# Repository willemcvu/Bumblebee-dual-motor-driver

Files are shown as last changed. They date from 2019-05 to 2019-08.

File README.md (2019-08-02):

**_NOTE: Everything here is still actively in development, and is mostly untested. Firmware has not been written; BOMs have not been created. If you'd like to use something here, I would suggest waiting until I have tested all hardware and written firmware._**

**All boards below will be available for sale bare or assembled at some point in the near future, likely on Tindie. For now, feel free to start an issue if you're interested in buying a board.**

Kicad and Arduino sources for the Bumblebee seris of Arduino-compatible dual-motor control boards, all designed to be retrofitable in the Fisher-Price WildThing to provide alternative control means for wheelchair adaption.

There are three different boards, each with discinct purposes.

# Bumblebee-board
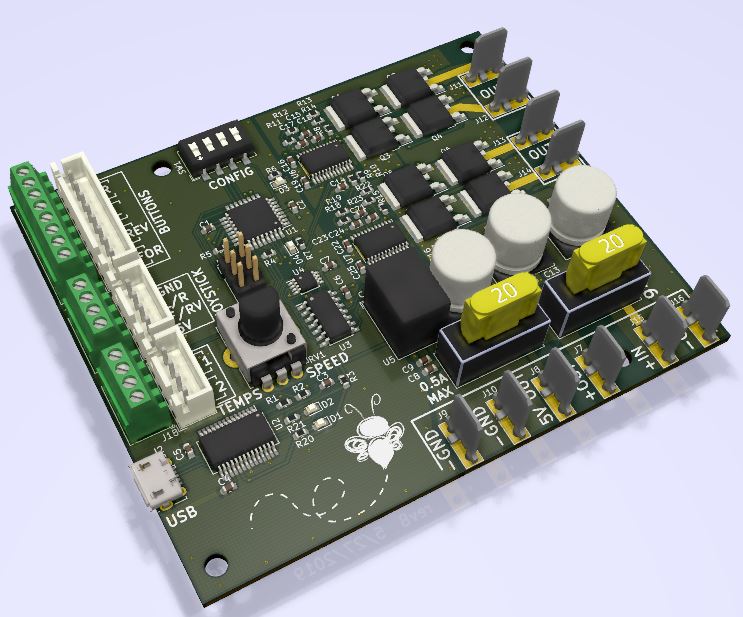
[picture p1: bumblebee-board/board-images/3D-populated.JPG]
bumblbee-board


This is the main board, and is designed to be a drop-in replacement of the stock WildThing control board. There are two complete H-bridge motor drivers using the A4940 motor driver. The uC is the AtMega328P, with an FTDI USB interface for complete Arduino functionaliy. Connectors for motor and power match those on the stock control board (they mate to standard 1/4" automotive blade terminals), so no crimping or soldering is needed.

Other features include:
* Dual inputs: buttons or joystick
* Choice of JST XH or screw terminals for button/joystick inputs
* On-the-fly configuration via DIP switch
* Potentiometer for speed limiting adjustment
* Built-in fusing
* Fused blade-type 12V and 5V outputs, as well as two extra grounds
* Instructions on the back, as well as Arduino pin equivelancies for the terminal blocks

This board has an operating voltage of 7V-24V, although the max could be raised by changing the 470uF caps to higher-voltage rated caps.

# Bumblebee-adapter
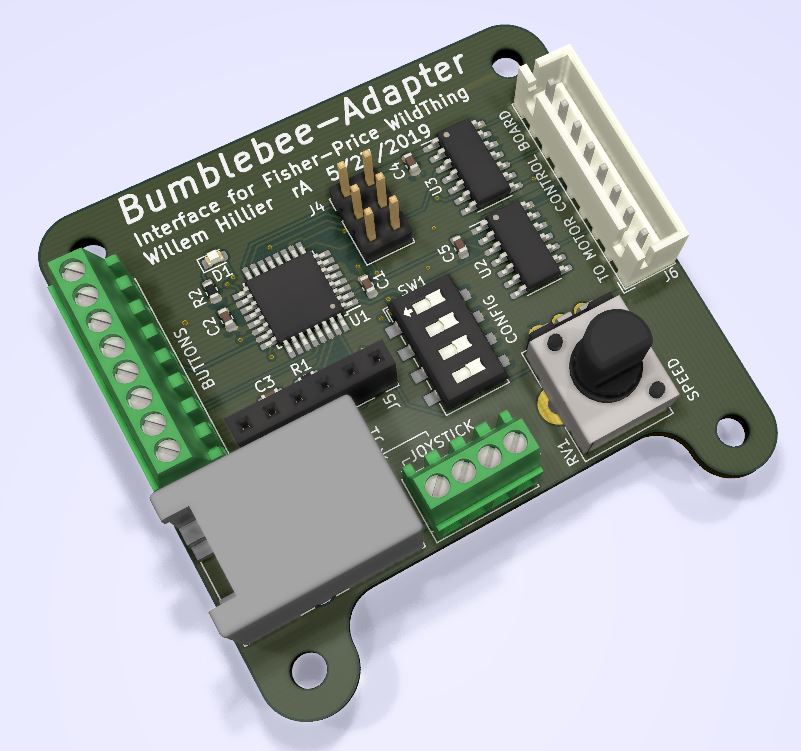
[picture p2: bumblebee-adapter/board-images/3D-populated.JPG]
bumblebee-adapter


This is probably the ultimate solution for a configurable, low-cost WildThing controller.

This board does not directly drive motors. Instead, it plugs into the joystick headers on the original control board and emulates their signals using two dual-channel SPI DACs. The speed limiting is still controllable via the original button under the seat using this method, and the seat safety switch remains intact.

It does not have onboard USB (due to cost), but has an "FTDI" port for easy programming/configuration with any generic USB-to-serial cable.

It also sports an RJ25 port for joystick input, in addition to a set of 2.54mm holes that can be used either for a terminal block or for a JST XH connector. I'll be designing a 3D-printable joystick unit with a matching RJ25 port at some point in the near future.

# Bumblebee-compact
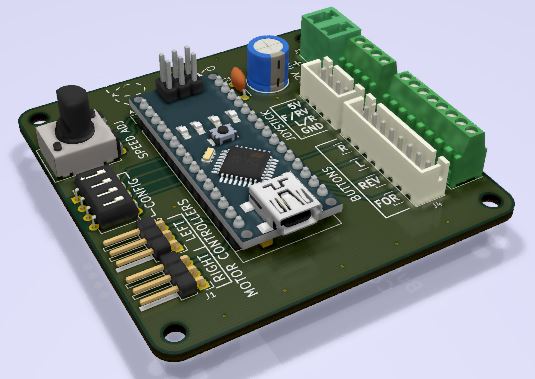
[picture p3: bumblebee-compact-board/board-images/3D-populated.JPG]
bumblebee-compact


This very simple board is designed to be a very low-cost, easy-to-solder board that drives external motor controllers, such as RC electronic speed controls (ESCs). All components are through-hole, and the total cost of assembling this should only be around $15.

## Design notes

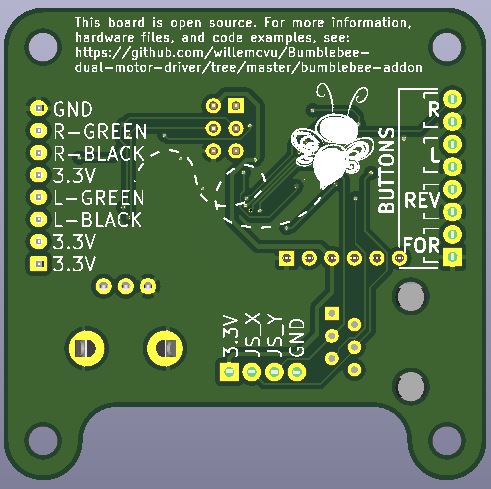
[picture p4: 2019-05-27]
bumblebee-adapter/board-images/back-populated.JPG

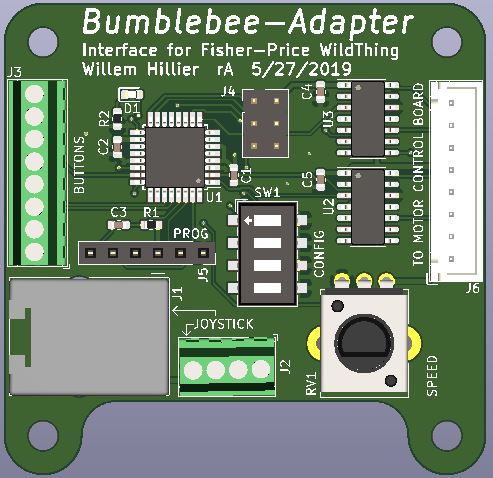
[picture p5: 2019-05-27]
bumblebee-adapter/board-images/front-populated.JPG

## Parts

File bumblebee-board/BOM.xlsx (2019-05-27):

Id | Designator | Package | Quantity | Designation | Manufacturer | PN
4 | J11 | TE_1217861-1 | 9 | MOTOR1_A | TE | 1217861-1
6 | C13,C11,C12 | C_Elec_10x10.2 | 3 | 470u |  | EEV477M025S9PAA
7 | C24,C25,C23,C17,C18,C19 | C_0603_1608Metric | 6 | 1u | NIC Components | NMC0603Y5V105Z16TRPF
8 | C22,C20,C1,C2,C3,C4,C5,C6,C7,C9,C10,C14,C16 | C_0603_1608Metric | 13 | 0.1u
9 | C21,C8,C15 | C_0603_1608Metric | 3 | 10u
10 | R19,R18,R16,R17,R10,R11,R12,R13 | R_0603_1608Metric | 8 | 27 | NIC Components | NRC06F27R0TRF
11 | U7,U6 | HTSSOP-24-1EP_4.4x7.8mm_P0.65mm_EP3.4x7.8mm_Mask2.4x4.68mm | 2 | A4940KLPTR-T | ALLEGRO | A4940KLPTR-T
12 | Q7,Q6,Q5,Q8,Q1,Q2,Q3,Q4 | TO-252-2 | 8 | Q_NMOS_GDS | Infineon | IRFR3410TRLPBF
15 | R14,R3,R4,R5,R8 | R_0603_1608Metric | 5 | 10k
16 | R15,R9 | R_0603_1608Metric | 2 | 82k | NIC Components | NRC06J823TRF
17 | D1 | LED_0603_1608Metric | 1 | RX
18 | D2 | LED_0603_1608Metric | 1 | TX
19 | D3,D4 | LED_0603_1608Metric | 2 | LED
20 | J5,J18 | JST_XH_B4B-XH-A_1x04_P2.50mm_Vertical | 2 | JST-XH
21 | J6 | JST_XH_B8B-XH-A_1x08_P2.50mm_Vertical | 1 | JST-XH
28 | R1,R2,R6,R7,R20,R21 | R_0603_1608Metric | 6 | 1k
29 | SW1 | SW_DIP_SPSTx04_Slide_6.7x11.72mm_W6.73mm_P2.54mm_LowProfile_Jpin | 1 | SW_DIP_x04 | CTS | 219-4LPST
30 | U1 | TQFP-32_7x7mm_P0.8mm | 1 | ATmega328P-AU
31 | U2 | SSOP-28_5.3x10.2mm_P0.65mm | 1 | FT232RL | FTDI | FT232RL-TUBE
32 | U3 | SOIC-14_3.9x8.7mm_P1.27mm | 1 | 74LS08 | Texas Instruments | SN74LS08D
33 | U4 | TSSOP-8_3x3mm_P0.65mm | 1 | 74LVC2G240 | Nexperia | 74LVC2G240DC,125
34 | U5 | Converter_DCDC_RECOM_R-78E-0.5_THT | 1 | R-78E5.0-0.5 | Recom | R-78E5.0-0.5
35 | J1 | PinHeader_2x03_P2.54mm_Vertical | 1 | ICSP
36 | F1,F2 | Fuseholder_Blade_Mini_Keystone_3568 | 2 | 0.5A
38 | J4 | TerminalBlock_TE_282834-8_1x08_P2.54mm_Horizontal | 1 | HEADER
39 | J3,J17 | TerminalBlock_TE_282834-4_1x04_P2.54mm_Horizontal | 2 | HEADER
40 | J2 | USB_Micro-B_Molex-105017-0001 | 1 | USB_B_Micro | Molex | 105017-0001
41 | RV1 | Potentiometer_Bourns_PTV09A-1_Single_Vertical | 1 | R_POT_US | Bourns | PTV09A-4020F-B103

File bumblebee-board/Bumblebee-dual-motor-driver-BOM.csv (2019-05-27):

Id | Designator | Package | Quantity | Designation | Supplier and ref
1 | G*** | vtLogo15mm | 1 | LOGO
2 | REF**,REF**,REF**,REF** | MountingHole_3.2mm_M3 | 4 | MountingHole_3.2mm_M3
3 | SW1 | dipLOGO | 1 | SW_DIP_x04
4 | J11 | TE_1217861-1 | 1 | MOTOR1_A
5 | G***,G*** | bumblebee_logo | 2 | LOGO
6 | C13,C11,C12 | C_Elec_10x10.2 | 3 | 470u
7 | C24,C25,C23,C17,C18,C19 | C_0603_1608Metric | 6 | 1u
8 | C22,C20,C1,C2,C3,C4,C5,C6,C7,C9,C10,C14,C16 | C_0603_1608Metric | 13 | 0.1u
9 | C21,C8,C15 | C_0603_1608Metric | 3 | 10u
10 | R19,R18,R16,R17,R10,R11,R12,R13 | R_0603_1608Metric | 8 | 27
11 | U7,U6 | HTSSOP-24-1EP_4.4x7.8mm_P0.65mm_EP3.4x7.8mm_Mask2.4x4.68mm | 2 | A4940KLPTR-T
12 | Q7,Q6,Q5,Q8,Q1,Q2,Q3,Q4 | TO-252-2 | 8 | Q_NMOS_GDS
13 | J13 | TE_1217861-1 | 1 | MOTOR2_A
14 | J14 | TE_1217861-1 | 1 | MOTOR2_B
15 | R14,R3,R4,R5,R8 | R_0603_1608Metric | 5 | 10k
16 | R15,R9 | R_0603_1608Metric | 2 | 82k
17 | D1 | LED_0603_1608Metric | 1 | RX
18 | D2 | LED_0603_1608Metric | 1 | TX
19 | D3,D4 | LED_0603_1608Metric | 2 | LED
20 | J5,J18 | JST_XH_B4B-XH-A_1x04_P2.50mm_Vertical | 2 | JST-XH
21 | J6 | JST_XH_B8B-XH-A_1x08_P2.50mm_Vertical | 1 | JST-XH
22 | J7 | TE_1217861-1 | 1 | 12V_OUT
23 | J8 | TE_1217861-1 | 1 | 5V_OUT
24 | J9,J10 | TE_1217861-1 | 2 | GND
25 | J12 | TE_1217861-1 | 1 | MOTOR1_B
26 | J15 | TE_1217861-1 | 1 | MAIN+
27 | J16 | TE_1217861-1 | 1 | MAIN-
28 | R1,R2,R6,R7,R20,R21 | R_0603_1608Metric | 6 | 1k
29 | SW1 | SW_DIP_SPSTx04_Slide_6.7x11.72mm_W6.73mm_P2.54mm_LowProfile_JPin | 1 | SW_DIP_x04
30 | U1 | TQFP-32_7x7mm_P0.8mm | 1 | ATmega328P-AU
31 | U2 | SSOP-28_5.3x10.2mm_P0.65mm | 1 | FT232RL
32 | U3 | SOIC-14_3.9x8.7mm_P1.27mm | 1 | 74LS08
33 | U4 | TSSOP-8_3x3mm_P0.65mm | 1 | 74LVC2G240
34 | U5 | Converter_DCDC_RECOM_R-78E-0.5_THT | 1 | R-78E5.0-0.5
35 | J1 | PinHeader_2x03_P2.54mm_Vertical | 1 | ICSP
36 | F1 | Fuseholder_Blade_Mini_Keystone_3568 | 1 | 0.5A
37 | F2 | Fuseholder_Blade_Mini_Keystone_3568 | 1 | 20A
38 | J4 | TerminalBlock_TE_282834-8_1x08_P2.54mm_Horizontal | 1 | HEADER
39 | J3,J17 | TerminalBlock_TE_282834-4_1x04_P2.54mm_Horizontal | 2 | HEADER
40 | J2 | USB_Micro-B_Molex-105017-0001 | 1 | USB_B_Micro
41 | RV1 | Potentiometer_Bourns_PTV09A-1_Single_Vertical | 1 | R_POT_US

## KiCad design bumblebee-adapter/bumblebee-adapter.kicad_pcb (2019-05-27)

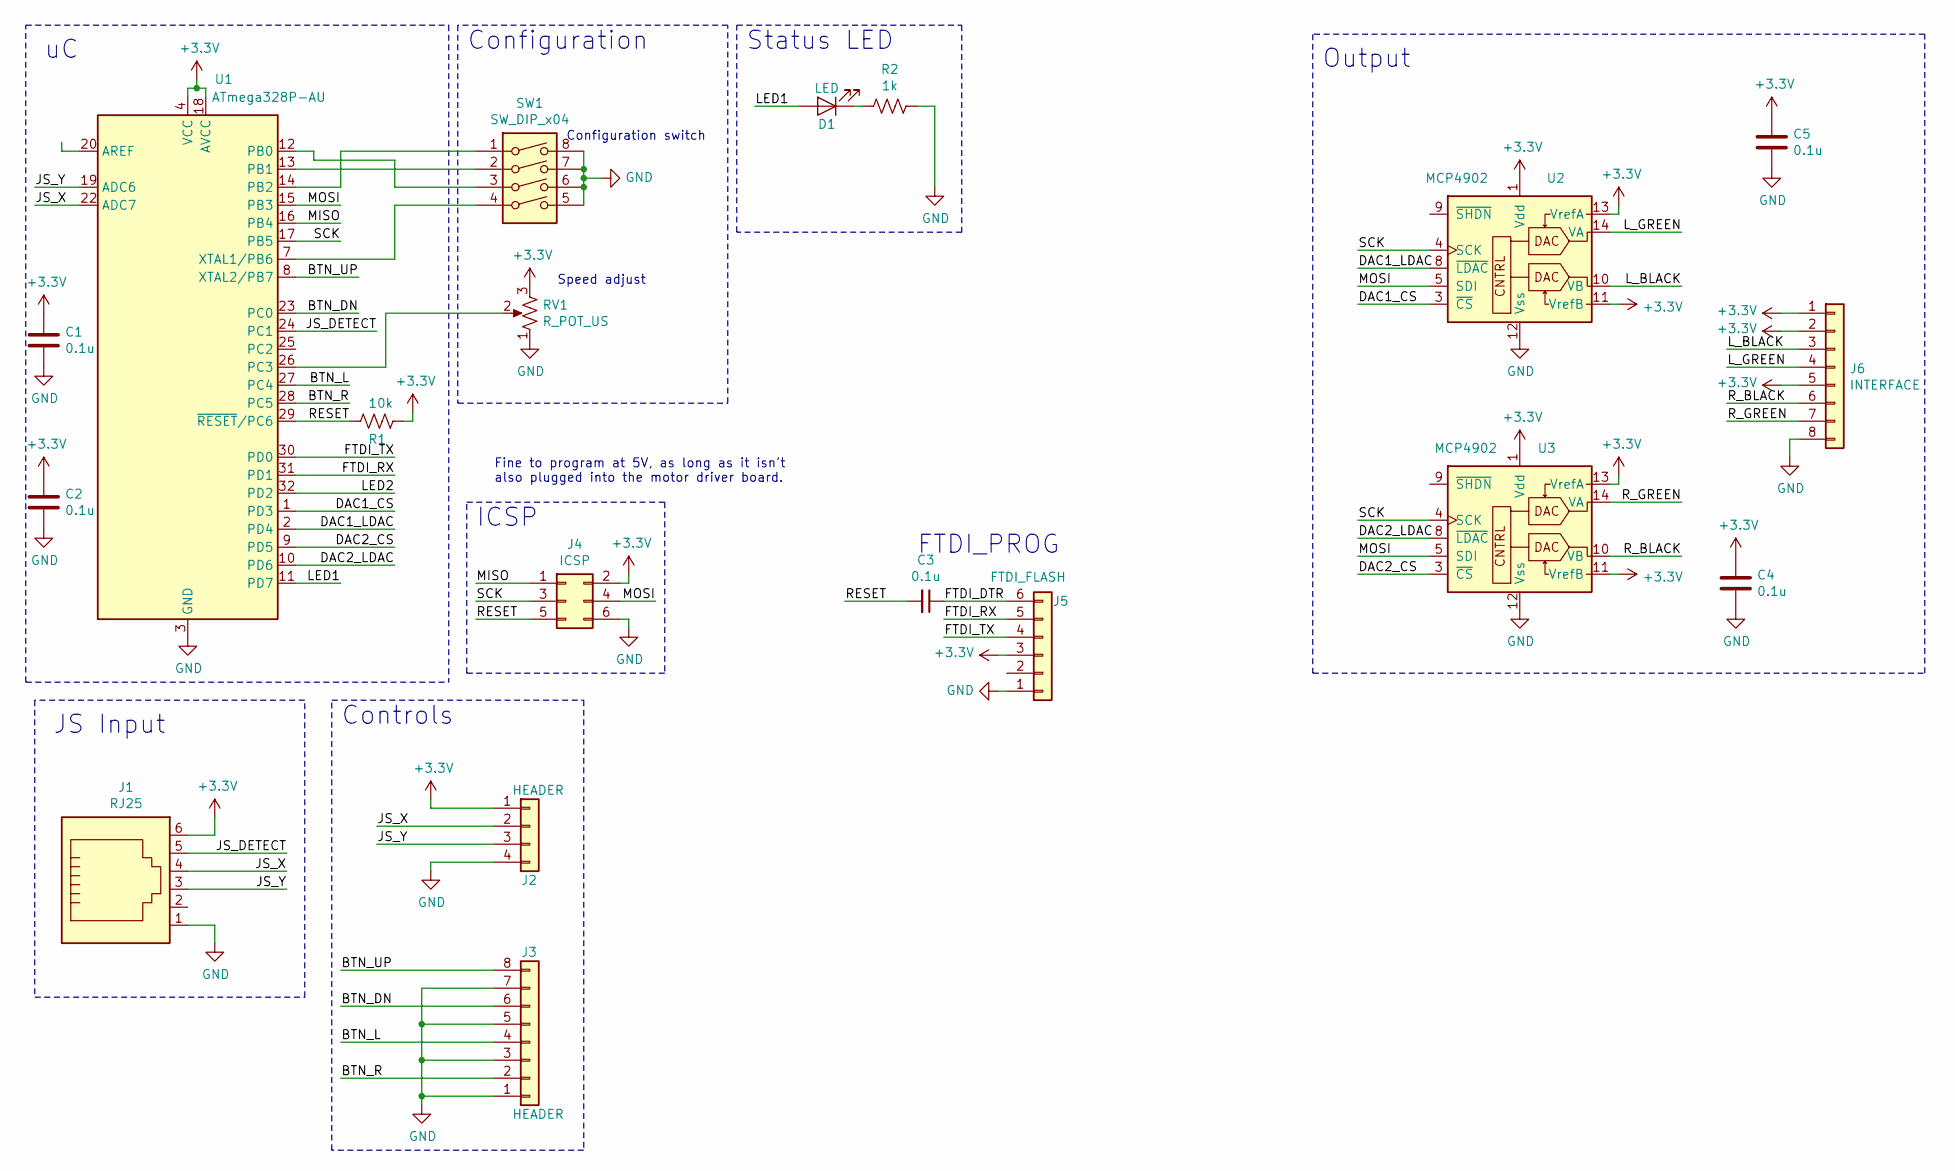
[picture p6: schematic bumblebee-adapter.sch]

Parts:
C1, C2, C3, C4, C5: 0.1u; C_0603_1608Metric
D1: LED; LED_0603_1608Metric
J1: RJ25; RJ12_Amphenol_54601
J2: HEADER; TerminalBlock_TE_282834-4_1x04_P2.54mm_Horizontal
J3: HEADER; TerminalBlock_TE_282834-8_1x08_P2.54mm_Horizontal
J4: ICSP; PinHeader_2x03_P2.54mm_Vertical
J5: FTDI_FLASH; PinSocket_1x06_P2.54mm_Vertical
J6: INTERFACE; JST_XH_B8B-XH-A_1x08_P2.50mm_Vertical
R1: 10k; R_0603_1608Metric
R2: 1k; R_0603_1608Metric
RV1: R_POT_US; Potentiometer_Bourns_PTV09A-1_Single_Vertical
SW1: SW_DIP_x04; SW_DIP_SPSTx04_Slide_6.7x11.72mm_W6.73mm_P2.54mm_LowProfile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
U1: ATmega328P-AU; TQFP-32_7x7mm_P0.8mm
U2, U3: MCP4902; SOIC-14_3.9x8.7mm_P1.27mm

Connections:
+3V3: C1.1, C2.1, C4.1, C5.1, J1.6, J2.1, J4.2, J5.3, J6.1, J6.2, J6.5, R1.1, RV1.3, U1.4 (VCC), U1.6 (VCC), U1.18 (AVCC), U2.1 (Vdd), U2.11 (VrefB), U2.13 (VrefA), U3.1 (Vdd), U3.11 (VrefB), U3.13 (VrefA)
/BTN_DN: J3.6, U1.23 (PC0)
/BTN_L: J3.4, U1.27 (PC4)
/BTN_R: J3.2, U1.28 (PC5)
/BTN_UP: J3.8, U1.8 (XTAL2/PB7)
/DAC1_CS: U1.1 (PD3), U2.3 (~CS)
/DAC1_LDAC: U1.2 (PD4), U2.8 (~LDAC)
/DAC2_CS: U1.9 (PD5), U3.3 (~CS)
/DAC2_LDAC: U1.10 (PD6), U3.8 (~LDAC)
/FTDI_DTR: C3.1, J5.6
/FTDI_RX: J5.5, U1.31 (PD1)
/FTDI_TX: J5.4, U1.30 (PD0)
/JS_DETECT: J1.5, U1.24 (PC1)
/JS_X: J1.4, J2.2, U1.22 (ADC7)
/JS_Y: J1.3, J2.3, U1.19 (ADC6)
/LED1: D1.2 (A), U1.11 (PD7)
/L_BLACK: J6.3, U2.10 (VB)
/L_GREEN: J6.4, U2.14 (VA)
/MISO: J4.1, U1.16 (PB4)
/MOSI: J4.4, U1.15 (PB3), U2.5 (SDI), U3.5 (SDI)
/RESET: C3.2, J4.5, R1.2, U1.29 (~RESET~/PC6)
/R_BLACK: J6.6, U3.10 (VB)
/R_GREEN: J6.7, U3.14 (VA)
/SCK: J4.3, U1.17 (PB5), U2.4 (SCK), U3.4 (SCK)
GND: C1.2, C2.2, C4.2, C5.2, J1.1, J2.4, J3.1, J3.3, J3.5, J3.7, J4.6, J5.1, J6.8, R2.1, RV1.1, SW1.5, SW1.6, SW1.7, SW1.8, U1.3 (GND), U1.5 (GND), U1.21 (GND), U2.12 (Vss), U3.12 (Vss)
unnamed: D1.1 (K), R2.2
unnamed: RV1.2, U1.26 (PC3)
unnamed: SW1.1, U1.14 (PB2)
unnamed: SW1.2, U1.13 (PB1)
unnamed: SW1.3, U1.12 (PB0)
unnamed: SW1.4, U1.7 (XTAL1/PB6)

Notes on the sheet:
ICSP
Status LED
Configuration switch
Speed adjust
Controls
Configuration
Fine to program at 5V, as long as it isn't also plugged into the motor driver board.
Output
JS Input
FTDI_PROG

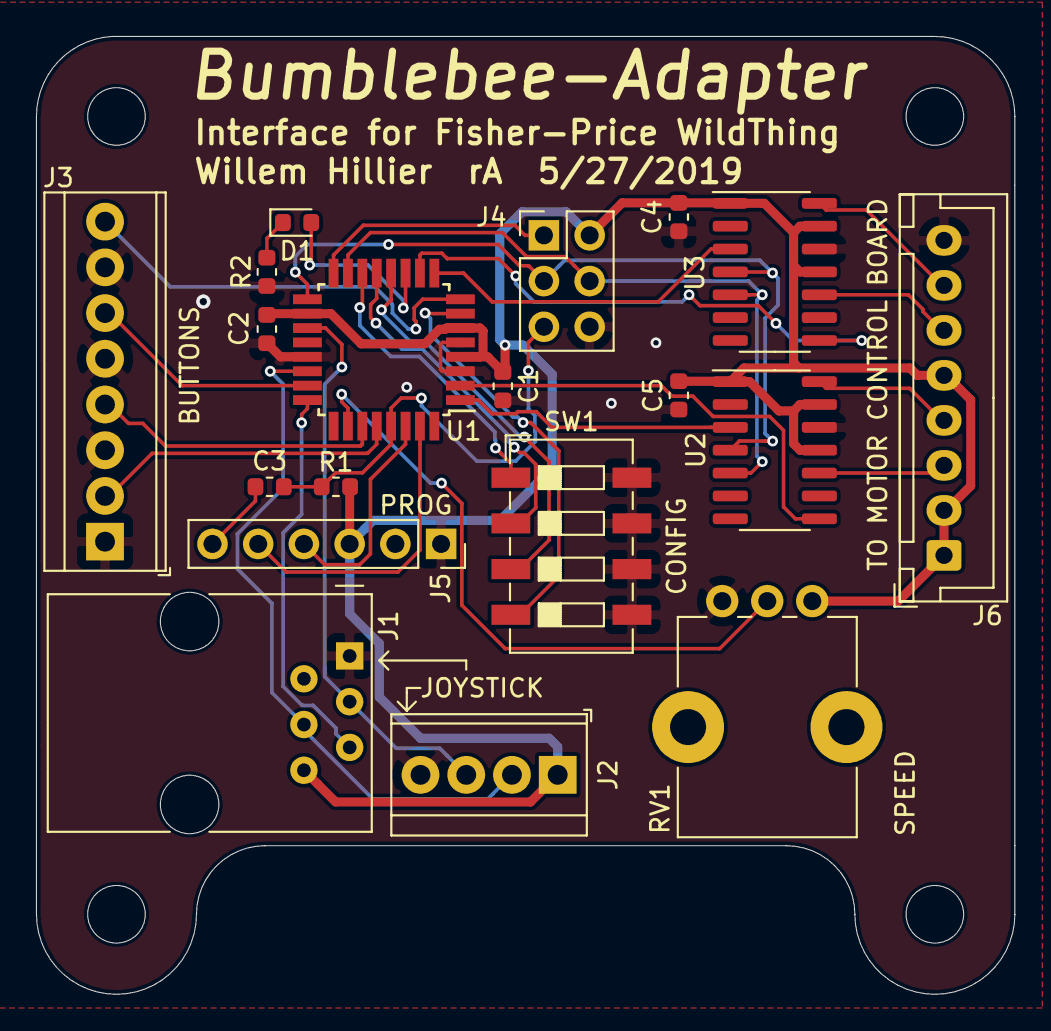
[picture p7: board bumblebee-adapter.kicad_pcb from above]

Board: 2 copper layers, 54.4 x 53.2 mm, 19 parts (0 on the bottom side), 31 nets.

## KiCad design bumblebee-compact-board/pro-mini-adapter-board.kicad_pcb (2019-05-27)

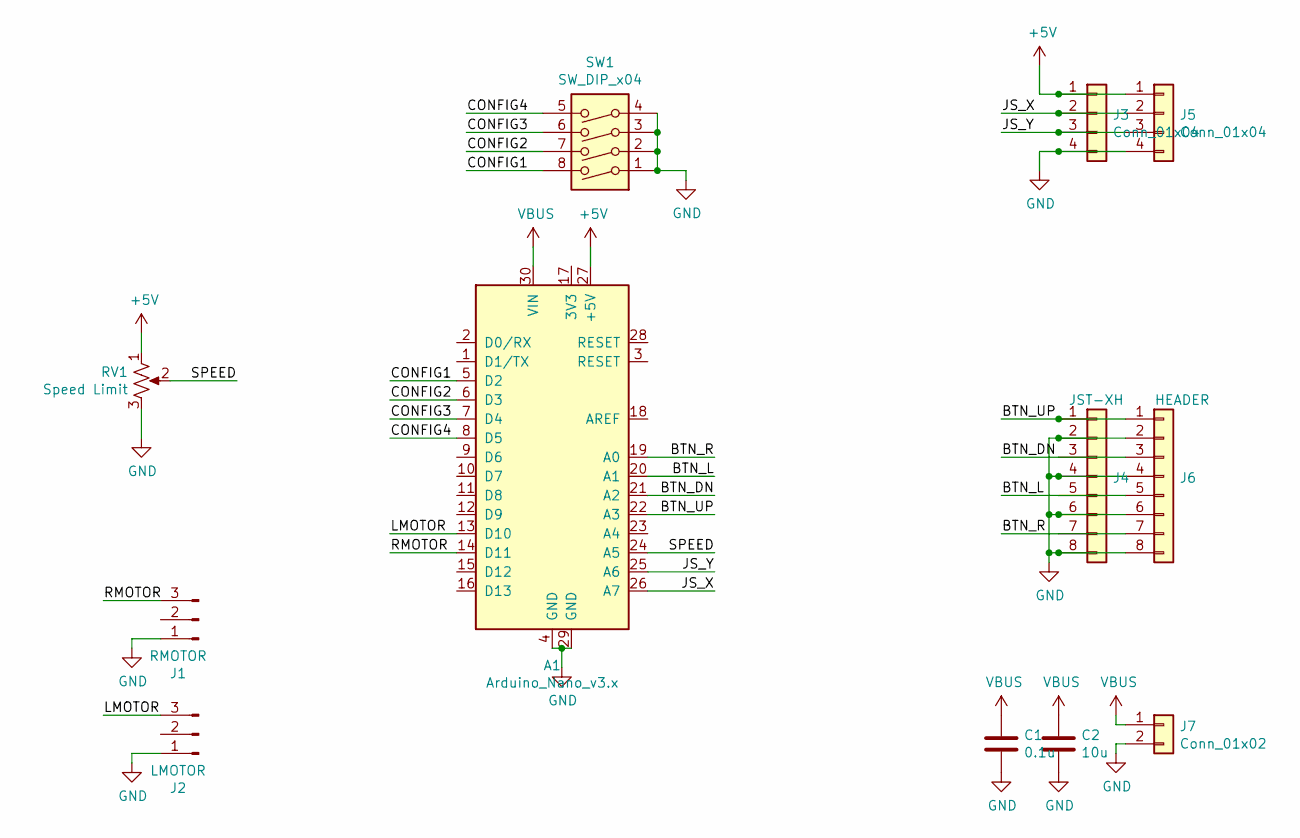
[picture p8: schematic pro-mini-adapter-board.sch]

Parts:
A1: Arduino_Nano_v3.x; Arduino_Nano
C1: 0.1u; C_Disc_D5.0mm_W2.5mm_P5.00mm
C2: 10u; C_Radial_D8.0mm_H7.0mm_P3.50mm
J1: RMOTOR; PinHeader_1x03_P2.54mm_Horizontal
J2: LMOTOR; PinHeader_1x03_P2.54mm_Horizontal
J3: Conn_01x04; JST_XH_B4B-XH-A_1x04_P2.50mm_Vertical
J4: JST-XH; JST_XH_B8B-XH-A_1x08_P2.50mm_Vertical
J5: Conn_01x04; TerminalBlock_TE_282834-4_1x04_P2.54mm_Horizontal
J6: HEADER; TerminalBlock_TE_282834-8_1x08_P2.54mm_Horizontal
J7: Conn_01x02; PhoenixContact_MCV_1,5_2-G-5.08_1x02_P5.08mm_Vertical
RV1: Speed Limit; Potentiometer_Bourns_PTV09A-1_Single_Vertical
SW1: SW_DIP_x04; SW_DIP_SPSTx04_Slide_6.7x11.72mm_W7.62mm_P2.54mm_LowProfile

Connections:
+5V: A1.27 (+5V), J3.1, J5.1, RV1.1
/BTN_DN: A1.21 (A2), J4.3, J6.3
/BTN_L: A1.20 (A1), J4.5, J6.5
/BTN_R: A1.19 (A0), J4.7, J6.7
/BTN_UP: A1.22 (A3), J4.1, J6.1
/CONFIG1: A1.5 (D2), SW1.8
/CONFIG2: A1.6 (D3), SW1.7
/CONFIG3: A1.7 (D4), SW1.6
/CONFIG4: A1.8 (D5), SW1.5
/JS_X: A1.26 (A7), J3.2, J5.2
/JS_Y: A1.25 (A6), J3.3, J5.3
/LMOTOR: A1.13 (D10), J2.3
/RMOTOR: A1.14 (D11), J1.3
/SPEED: A1.24 (A5), RV1.2
GND: A1.4 (GND), A1.29 (GND), C1.2, C2.2, J1.1, J2.1, J3.4, J4.2, J4.4, J4.6, J4.8, J5.4, J6.2, J6.4, J6.6, J6.8, J7.2, RV1.3, SW1.1, SW1.2, SW1.3, SW1.4
VBUS: A1.30 (VIN), C1.1, C2.1, J7.1

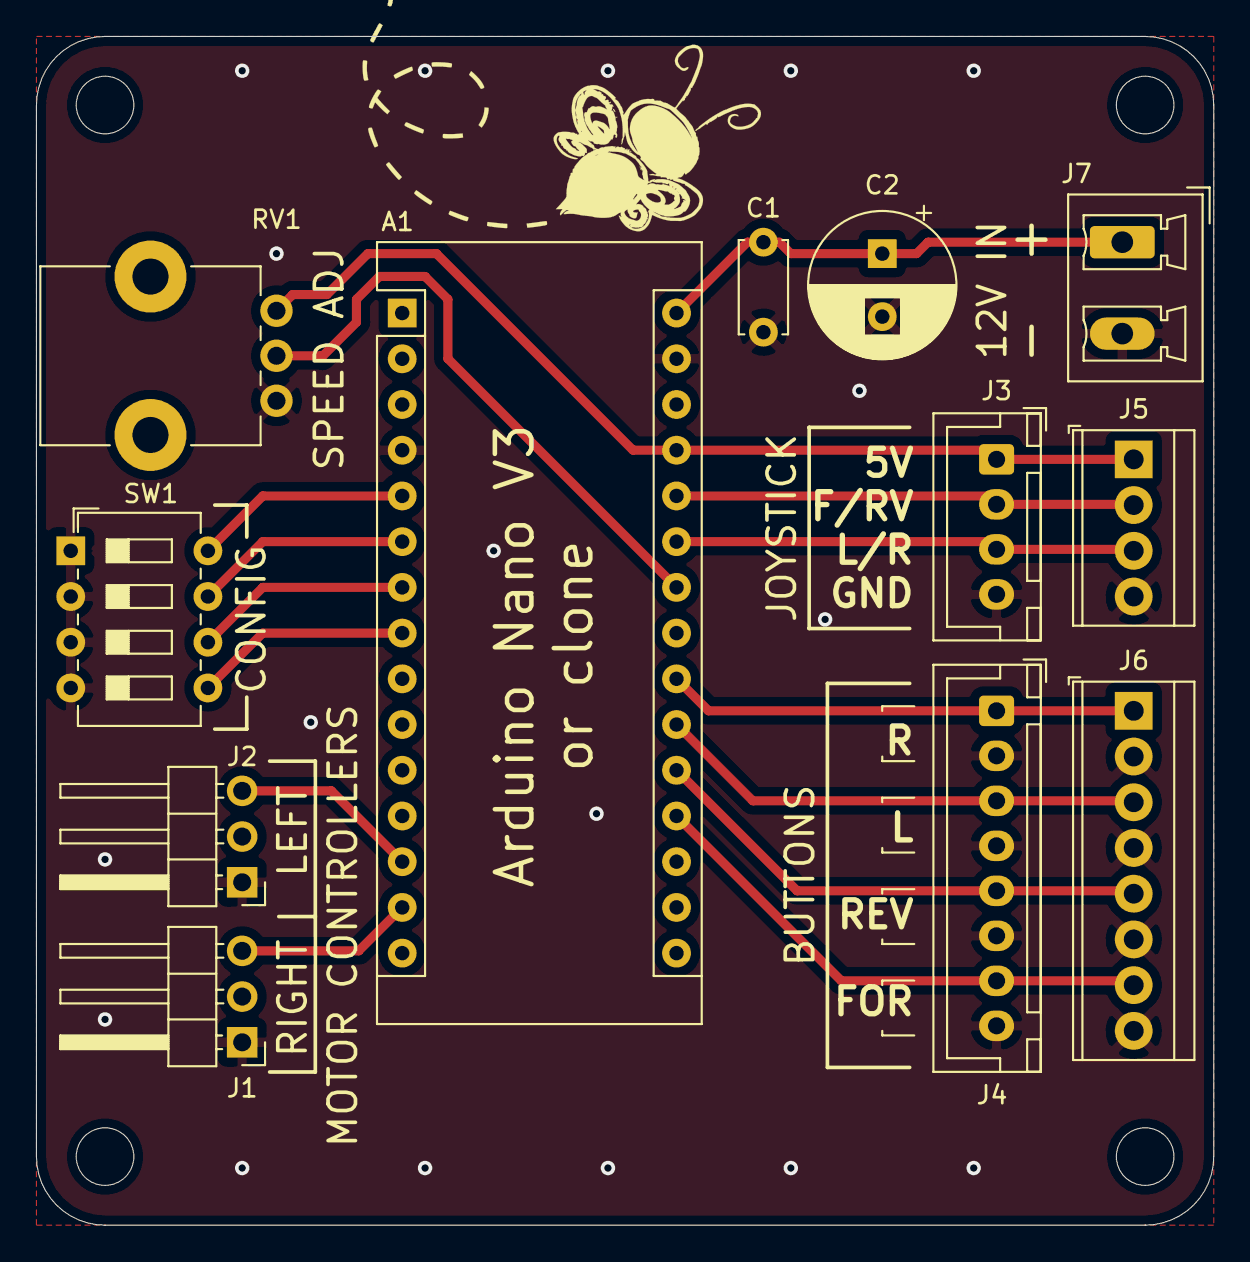
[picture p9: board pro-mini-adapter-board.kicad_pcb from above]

Board: 2 copper layers, 65.4 x 66.0 mm, 12 parts (0 on the bottom side), 16 nets.

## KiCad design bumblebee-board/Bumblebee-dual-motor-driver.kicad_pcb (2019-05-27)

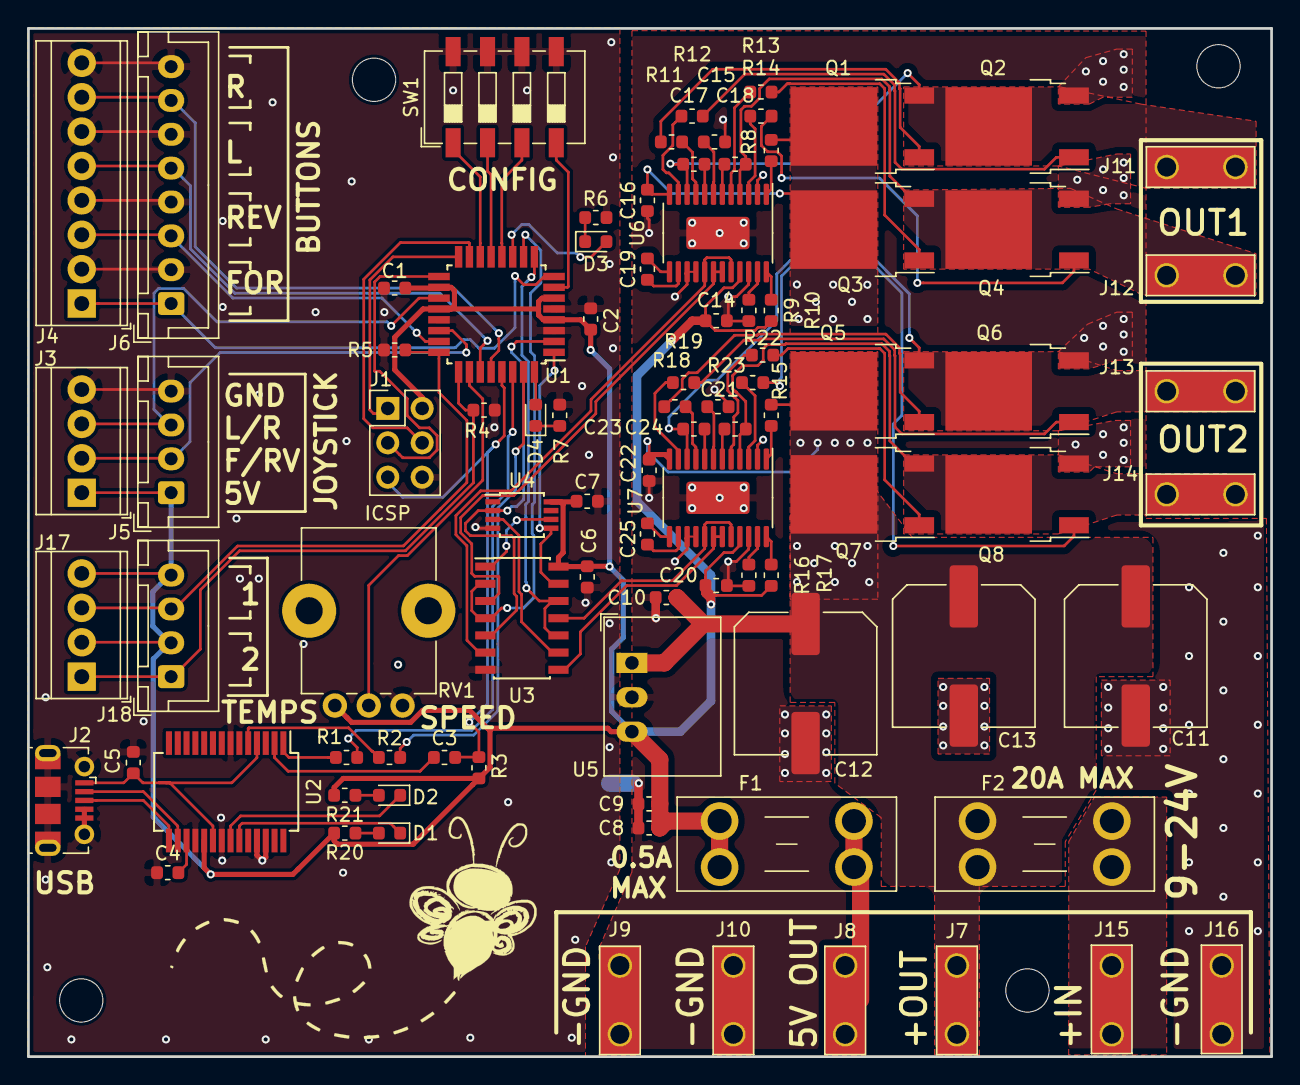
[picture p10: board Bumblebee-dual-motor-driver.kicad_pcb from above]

Board: 2 copper layers, 91.8 x 75.9 mm, 90 parts (1 on the bottom side), 85 nets.

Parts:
C1, C2, C3, C4, C5, C6, C7, C9, C10, C14, C16, C20, C22: 0.1u; C_0603_1608Metric
C8, C15, C21: 10u; C_0603_1608Metric
C11, C12, C13: 470u; C_Elec_10x10.2
C17, C18, C19, C23, C24, C25: 1u; C_0603_1608Metric
D1: RX; LED_0603_1608Metric
D2: TX; LED_0603_1608Metric
D3, D4: LED; LED_0603_1608Metric
F1: 0.5A; Fuseholder_Blade_Mini_Keystone_3568
F2: 20A; Fuseholder_Blade_Mini_Keystone_3568
J1: ICSP; PinHeader_2x03_P2.54mm_Vertical
J2: USB_B_Micro; USB_Micro-B_Molex-105017-0001
J3, J17: HEADER; TerminalBlock_TE_282834-4_1x04_P2.54mm_Horizontal
J4: HEADER; TerminalBlock_TE_282834-8_1x08_P2.54mm_Horizontal
J5, J18: JST-XH; JST_XH_B4B-XH-A_1x04_P2.50mm_Vertical
J6: JST-XH; JST_XH_B8B-XH-A_1x08_P2.50mm_Vertical
J7: 12V_OUT; TE_1217861-1
J8: 5V_OUT; TE_1217861-1
J9, J10: GND; TE_1217861-1
J11: MOTOR1_A; TE_1217861-1
J12: MOTOR1_B; TE_1217861-1
J13: MOTOR2_A; TE_1217861-1
J14: MOTOR2_B; TE_1217861-1
J15: MAIN+; TE_1217861-1
J16: MAIN-; TE_1217861-1
Q1, Q2, Q3, Q4, Q5, Q6, Q7, Q8: Q_NMOS_GDS; TO-252-2
R1, R2, R6, R7, R20, R21: 1k; R_0603_1608Metric
R3, R4, R5, R9, R16: 10k; R_0603_1608Metric
R8, R15: 27k; R_0603_1608Metric
R10, R17: 82k; R_0603_1608Metric
R11, R12, R13, R14, R18, R19, R22, R23: 27; R_0603_1608Metric
RV1: R_POT_US; Potentiometer_Bourns_PTV09A-1_Single_Vertical
SW1: SW_DIP_x04; dipLOGO
SW1#2: SW_DIP_x04; SW_DIP_SPSTx04_Slide_6.7x11.72mm_W6.73mm_P2.54mm_LowProfile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
U1: ATmega328P-AU; TQFP-32_7x7mm_P0.8mm
U2: FT232RL; SSOP-28_5.3x10.2mm_P0.65mm
U3: 74LS08; SOIC-14_3.9x8.7mm_P1.27mm
U4: 74LVC2G240; TSSOP-8_3x3mm_P0.65mm
U5: R-78E5.0-0.5; Converter_DCDC_RECOM_R-78E-0.5_THT
U6, U7: A4940KLPTR-T; HTSSOP-24-1EP_4.4x7.8mm_P0.65mm_EP3.4x7.8mm_Mask2.4x4.68mm

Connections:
+5V: C1.1, C2.1, C6.1, C7.1, C8.1, C9.1, C14.1, C20.1, F1.1, J1.2, J3.1, J5.1, J17.2, J17.4, J18.2, J18.4, R3.1, R9.1, R16.1, R20.2, R21.2, RV1.3, U1.4, U1.6, U1.18, U1.20, U2.19, U3.14, U4.8, U5.3, U6.21, U7.21
/BTN_DN: J4.3, J6.3, U1.23
/BTN_L: J4.5, J6.5, U1.27
/BTN_R: J4.7, J6.7, U1.28
/BTN_UP: J4.1, J6.1, U1.8
/JS_X: J3.2, J5.2, U1.22
/JS_Y: J3.3, J5.3, U1.19
/LED1: D3.2, U1.11
/LED2: D4.2, U1.32
/M8RXD: R1.2, U1.30
/M8TXD: R2.2, U1.31
/MISO: J1.1, U1.16
/MOSI: J1.4, U1.15
/MOTOR1_A: C17.1, J11.1, Q1.3, Q2.2, U6.10
/MOTOR1_B: C18.1, J12.1, Q3.3, Q4.2, U6.4
/MOTOR1_DIR: U1.2, U3.5, U4.2
/MOTOR1_DRIVER/AHI: U3.6, U6.17, U6.20
/MOTOR1_DRIVER/ALO: U3.3, U6.18, U6.19
/MOTOR1_DRIVER/~FAULT: R9.2, U6.24
/MOTOR1_DRIVER/~RESET: R8.1, U6.1
/MOTOR1_PWM: U1.10, U3.2, U3.4
/MOTOR2_A: C23.1, J13.1, Q5.3, Q6.2, U7.10
/MOTOR2_B: C24.1, J14.1, Q7.3, Q8.2, U7.4
/MOTOR2_DIR: U1.1, U3.13, U4.5
/MOTOR2_DRIVER/AHI: U3.11, U7.17, U7.20
/MOTOR2_DRIVER/ALO: U3.8, U7.18, U7.19
/MOTOR2_DRIVER/~FAULT: R16.2, U7.24
/MOTOR2_DRIVER/~RESET: R15.1, U7.1
/MOTOR2_PWM: U1.9, U3.10, U3.12
/NTC1: J17.1, J18.1, R4.2, U1.25
/NTC2: J17.3, J18.3, R5.2, U1.24
/RESET: C3.2, J1.5, R3.2, U1.29
/SCK: J1.3, U1.17
/USB_PWR: C5.1, J2.1, U2.4, U2.20
GND: C1.2, C2.2, C4.1, C5.2, C6.2, C7.2, C8.2, C9.2, C10.2, C11.2, C12.2, C13.2, C14.2, C15.2, C16.1, C20.2, C21.2, C22.1, J1.6, J2.4, J2.5, J2.6, J3.4, J4.2, J4.4, J4.6, J4.8, J5.4, J6.2, J6.4, J6.6, J6.8, J9.1, J10.1, J16.1, Q2.3, Q4.3, Q6.3, Q8.3, R4.1, R5.1, R6.1, R7.1, R10.2, R17.2, RV1.1, SW1#2.5, SW1#2.6, SW1#2.7, SW1#2.8, U1.3, U1.5, U1.21, U2.7, U2.18, U2.21, U2.25, U2.26, U3.7, U4.4, U5.2, U6.2, U6.15, U6.16, U6.22, U6.25, U7.2, U7.15, U7.16, U7.22, U7.25
unnamed: C3.1, U2.2
unnamed: C4.2, U2.17
unnamed: C15.1, U6.7
unnamed: C17.2, U6.8
unnamed: C18.2, U6.6
unnamed: C19.1, U6.14
unnamed: C19.2, U6.13
unnamed: C21.1, U7.7
unnamed: C23.2, U7.8
unnamed: C24.2, U7.6
unnamed: C25.1, U7.14
unnamed: C25.2, U7.13
unnamed: D1.1, U2.23
unnamed: D1.2, R20.1
unnamed: D2.1, U2.22
unnamed: D2.2, R21.1
unnamed: D3.1, R6.2
unnamed: D4.1, R7.2
unnamed: F1.2, J8.1
unnamed: F2.2, J15.1
unnamed: J2.2, U2.16
unnamed: J2.3, U2.15
unnamed: Q1.1, R11.1
unnamed: Q2.1, R12.1
unnamed: Q3.1, R13.1
unnamed: Q4.1, R14.1
unnamed: Q5.1, R18.1
unnamed: Q6.1, R19.1
unnamed: Q7.1, R22.1
unnamed: Q8.1, R23.1
unnamed: R1.1, U2.1
unnamed: R2.1, U2.5
unnamed: R10.1, U6.23
unnamed: R11.2, U6.9
unnamed: R12.2, U6.11
unnamed: R13.2, U6.5
unnamed: R14.2, U6.3
unnamed: R17.1, U7.23
unnamed: R18.2, U7.9
unnamed: R19.2, U7.11
unnamed: R22.2, U7.5
unnamed: R23.2, U7.3
unnamed: RV1.2, U1.26
unnamed: SW1#2.1, U1.14
unnamed: SW1#2.2, U1.13
unnamed: SW1#2.3, U1.12
unnamed: SW1#2.4, U1.7
unnamed: U3.1, U4.6
unnamed: U3.9, U4.3
VBUS: C10.1, C11.1, C12.1, C13.1, C16.2, C22.2, F2.1, J7.1, Q1.2, Q3.2, Q5.2, Q7.2, R8.2, R15.2, U5.1, U6.12, U7.12

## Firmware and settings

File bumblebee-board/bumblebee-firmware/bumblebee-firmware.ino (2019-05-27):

#define MOTOR1_DIR 4
#define MOTOR1_PWM 3
#define MOTOR2_DIR 6
#define MOTOR2_PWM 5

#define LOOP_DELAY 32
void setup() {
  //PWM frequency set up
  //TCCR2B = TCCR2B & B11111000 | B00000010; // D3 and D11, for PWM frequency of 3921.16 Hz
  //TCCR0B = TCCR0B & B11111000 | B00000010; // D5 and D6, for PWM frequency of 7812.50 Hz

  //Outputs
  pinMode(MOTOR1_DIR,OUTPUT);
  pinMode(MOTOR1_PWM,OUTPUT);
  pinMode(MOTOR2_DIR,OUTPUT);
  pinMode(MOTOR2_PWM,OUTPUT);
}

void loop() {
  //Test ramp motor forward/backwards
  
   digitalWrite(MOTOR2_DIR,1);

  //ramp up
  for(int i=0;i<256;i=i+LOOP_DELAY){
    analogWrite(MOTOR2_PWM,i);
    delay(100);
  }

  //ramp down
  for(int i=256;i>0;i=i-LOOP_DELAY){
    analogWrite(MOTOR2_PWM,i);
    delay(100);
  }

  //backwards
  digitalWrite(MOTOR2_DIR,0);

  //ramp up
  for(int i=0;i<256;i=i+LOOP_DELAY){
    analogWrite(MOTOR2_PWM,i);
    delay(100);
  }

  //ramp down
  for(int i=256;i>0;i=i-LOOP_DELAY){
    analogWrite(MOTOR2_PWM,i);
    delay(100);
  }


}

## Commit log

2019-05-08 Schematics fully drawn.
    [Bumblebee-dual-motor-driver.kicad_pcb, Bumblebee-dual-motor-driver.sch, file5CDA5614.sch]
2019-05-08 Assigned all footprints.
    Still need to pick and check FET footprint, pick pot.
    [Bumblebee-dual-motor-driver.sch, file5CDA5614.sch]
2019-05-08 Started moving components around on PCB.
    [Bumblebee-dual-motor-driver.sch, file5CDA5614.sch]
2019-05-08 Fixed small issues and started laying out H-bridge
    [Bumblebee-dual-motor-driver.kicad_pcb, Bumblebee-dual-motor-driver.sch, file5CDA5614.sch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]
2019-05-08 Layed out single H-bridge, started copying to the other H-bridge
    [Bumblebee-dual-motor-driver.kicad_pcb]
2019-05-09 Further progress laying out Bumblebee
    [Bumblebee-dual-motor-driver.kicad_pcb, Bumblebee-dual-motor-driver.sch, file5CDA5614.sch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]
2019-05-09 Finished routing board. Need to still do documentation.
    [Bumblebee-dual-motor-driver.kicad_pcb, Bumblebee-dual-motor-driver.sch]
2019-05-10 Done with silkscreen
    TODO: Add keepout areas on high-current traces
    [Bumblebee-dual-motor-driver.kicad_pcb, Bumblebee-dual-motor-driver.sch, file5CDA5614.sch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]
2019-05-11 Made bumblebee-compact. Added VT logo to both. Made gerbers. Shipping.
    [Bumblebee-dual-motor-driver-B_Cu.gbr, Bumblebee-dual-motor-driver-B_Mask.gbr, Bumblebee-dual-motor-driver-B_Paste.gbr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]
2019-05-12 Created initial BOM
    [Bumblebee-dual-motor-driver-BOM.csv]
2019-05-27 Started work on bumblebee-addon
    [bumblebee-addon.sch]
2019-05-27 Bumblebee-board r2 ready to ship.
    [BOM.csv, BOM.xlsx, Bumblebee-dual-motor-driver.kicad_pcb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]
2019-05-27 Shipped new revs of all boards.
    [Bumblebee-dual-motor-driver-B_Cu.gbr, Bumblebee-dual-motor-driver-B_Mask.gbr, Bumblebee-dual-motor-driver-B_Paste.gbr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]
2019-05-27 Added board images, cleaned up.
    [BOM.csv, OLD_BOM.xlsx]
2019-05-28 Renamed all files to bumblebee-adapter
    [bumblebee-adapter.kicad_pcb, bumblebee-adapter.sch, file5CEAA293.sch]
